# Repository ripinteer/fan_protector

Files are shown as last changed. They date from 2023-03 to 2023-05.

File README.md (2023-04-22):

# Fan Protector
Simple polulu-compatible protection board for Xiaomi/Roborock radial fans

### A word about all that hustle
>Remote cooling systems are becoming a trend in the field of high-end 3D printers. You install a big and powerful turbine somewhere on the printer and connect it to the tool head using a lightweight and flexible hose that you can purchase as a spare part for CPAP medical devices.
>
>Some DIY projects utilize big 7040 blowers for that purpose. 7040 is a BLDC fan with an external control board which is sold as a kit. Has pretty much power and costs about 50$ (which is quite steep for this kind of product imho)
>
>Turns out there are compact fans for robot vacuum cleaners, widely available on Aliexpress and other places as a spare parts. Provided in the refurbished condition they are five times cheaper than 7040, and still have comparable potential.

So if you want to adapt cheap (10$) and powerful vacuum cleaner turbines to your CPAP cooling system you can just connect PWM and DC to it... ~~Most likely it will burn your electronics and finally set you free from 3D printing addiciton~~ <br> **However, this type of connnection is strongly prohibited**, as it may (**will**) **fry** your **equipment** due to lack of certian passive components which is expected to be at the motherboard side.

For more details about XiaoFans aka Roborockers, please refer to <a href="https://github.com/condottab/Roborock-CPAP" target="_blank">this repo from a friend of mine</a>

My take on that situation
---
So, to make use of XiaoFan, good folks designed a simple schematic that adds missed protection features and stabilizes control voltage. To simplify the installation process and eliminate wiring "fun" I designed this simple polulu-compatible protection board, based on the original schematic.

<figure>
    <p align="center">
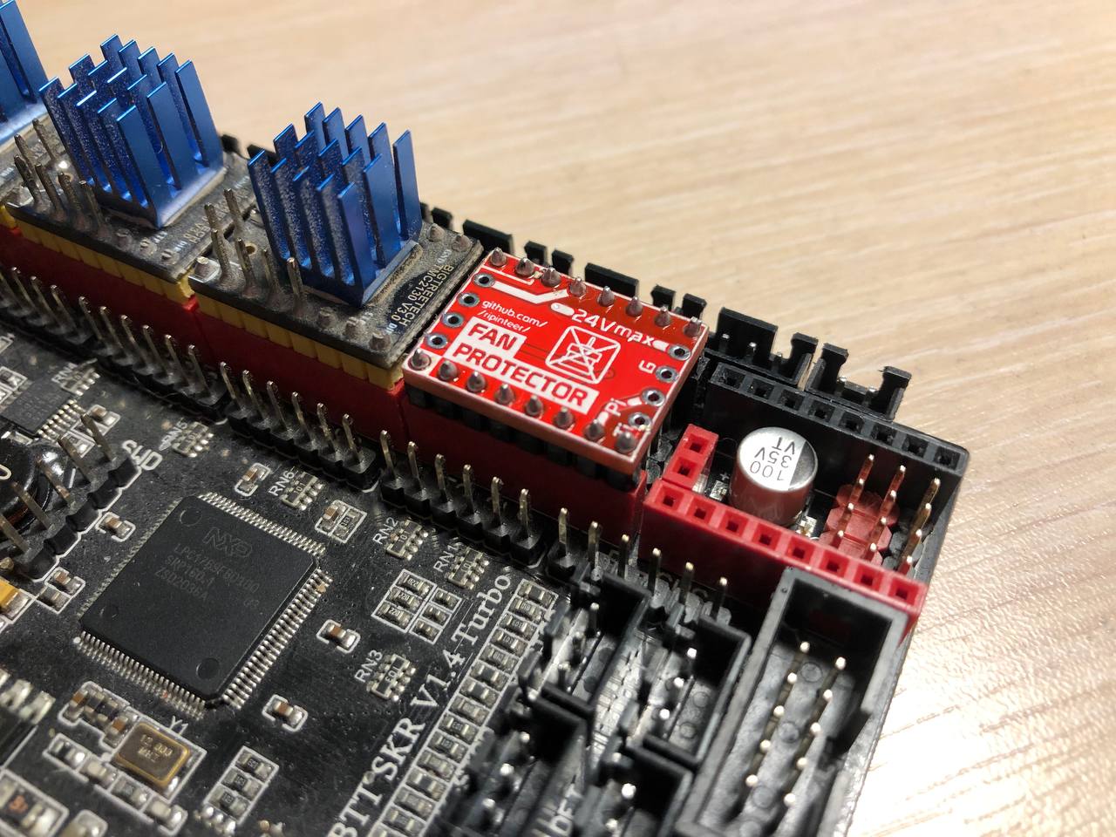
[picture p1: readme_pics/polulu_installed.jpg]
protector installed in polulu socket
        
    </p>
    <figcaption> <p align="center">As description suggests, protector can be installed right in the driver socket of the motherboard</p></figcaption>
</figure>

Once the board is installed, the corresponding 4pin XH2.54 motor connector becomes the protected fan connector. **It will use the same power source your steppers powered from, so keep that in mind.** The XiaoFan is rated 15V max, but it can be overvolted to 24V and tuned down to ~60% using PWM to continious run. 

> :pushpin: **Note:** This fan is a beast, so 60% of it will be already overkill for some cases

However, if you are reading this, you probably want to squeeze all from the XiaoFan setup, and this won't be a problem. Just to be safe you can provide some sort of cooling to the cooling fan (haha). The 40mm fan can be a way to go (refer to the link in the beginning).

### Connecting to Klipper
Nothing too complicated, just add another fan section. You can find examples for Qinatsu and Nidec (indicated at blower PCB) fans by using link above. 

* #### For polulu connection
you will need to know STEP and DIR pin addresses for the driver slot, where Fan Protector is installed. STEP pin serves as PWM and DIR serves as FG pin (tachometer, probably useless, and will be moved to another pin in Fan Protector v2.0 for Nidec workaround)

* #### For inline/"classic" connection
you will need to connect three (four with FG) pins: GND, VDD (aka VDD aka "plus"), and PWM. The XiaoFans is pretty powerhungry (~2.5A at 24V 100%) so you should power it from the main DC supply (PSU). PWM pin should be connected to any unoccupied PWM-controllable output on the motherboard. Ideally, this pin should support hardware PWM, so you can go for higher frequencies to eliminate "whistle" caused by low-freq PWM. Klipper should warn you if the chosen pin is unsupported by hardware PWM. <br> *Also this type of connection is already described in the repo by the link above which should be considered prior*

<figure>
    <p align="center">
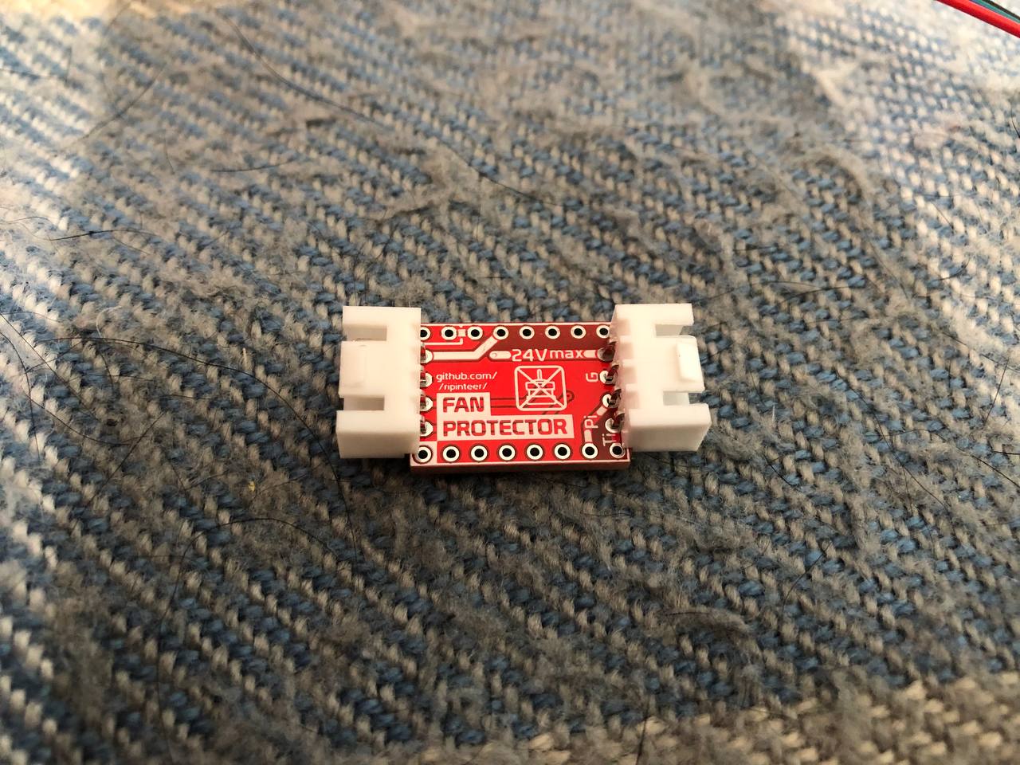
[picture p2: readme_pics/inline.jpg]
protector board with XH2.54 connectors installed
        
    </p>
    <figcaption><p align="center">Protector board with soldered XH2.54 connectors</p></figcaption>
</figure>

### Connecting to Marlin

Not yet tested/proved, but should be done with pin remapping according to scheme. TODO

---

### The Nidec case
As you can see, making use of this kind of tech comes with certain bumps. This time, it's Nidec fan tricky startup sequence. For some reason, they require a PWM signal to be present when powering it up. In other words, the PWM signal and DC power should be supplied together at the same moment. If not, Nidec won't start. Thankfully, Klipper comes with `enable_pin:` functionality, therefore we can just put a MOSFET in the DC circuit and tell Klipper about it.<br>
The only problem is my design doesn't have this MOSFET. "Why?" you ask. :eye:4:goat: <br>... Well, I guess that's what ver2.0 is for <br>
However! This only means that Nidec XiaoFans aren't supported by polulu configuration, but classic connection scheme is still viable. <br> No, lol. <br> **Nidec fans aren't supported at all (at least now)**, I need to finish *fan_protector v2.0* based on my custom scheme ASAP. <br> ~~For now you can power the fan through the one of exsiting heater MOSFETs on the motherboard, like additional heater port, which should be capable of driving 2.5+ Amps continuously. Set it's pin as `enable_pin:` in Klipper, connect the PWM and you should be good to go~~
> :pushpin: **Note:** As you can probably notice, this design supports both polulu and standart connection. Let's consider standart connection a default variant by now. 

<figure>
    <p align="center">
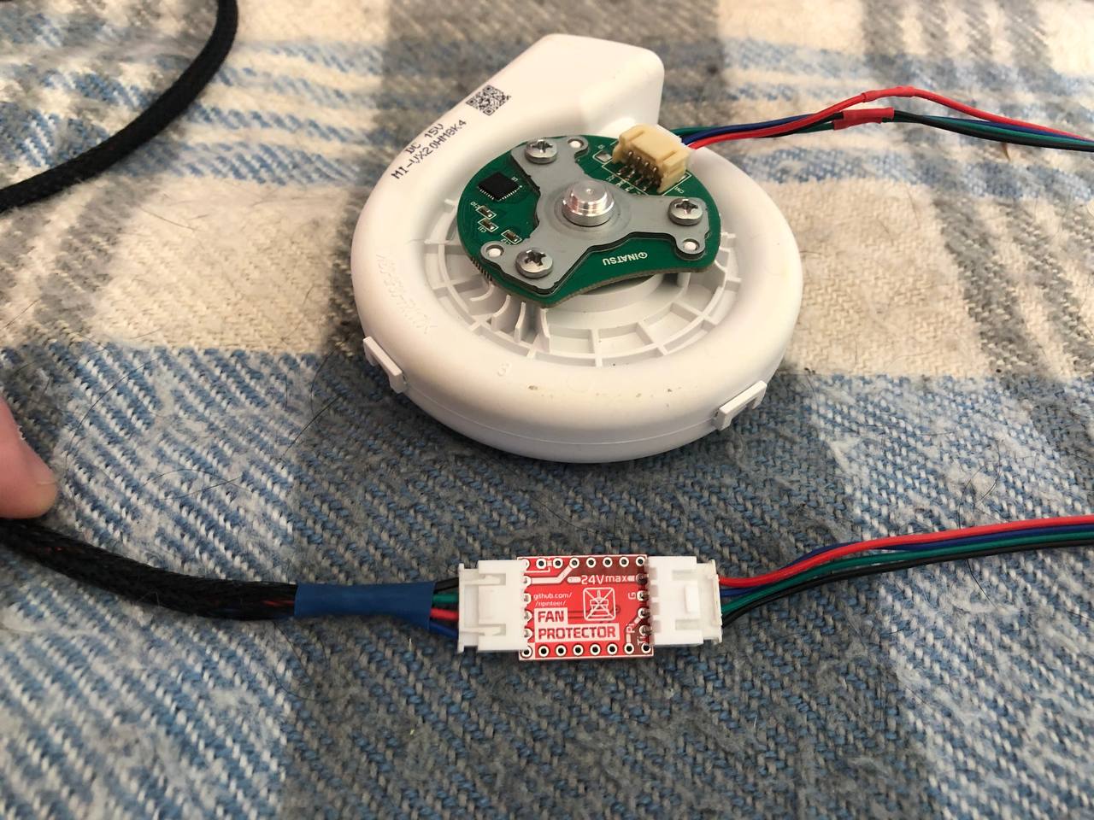
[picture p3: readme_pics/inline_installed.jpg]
Protector installed inline
        
    </p>
    <figcaption><p align="center">Inline connection example</p></figcaption>
</figure>

Any use of the provided files is at your own risk!

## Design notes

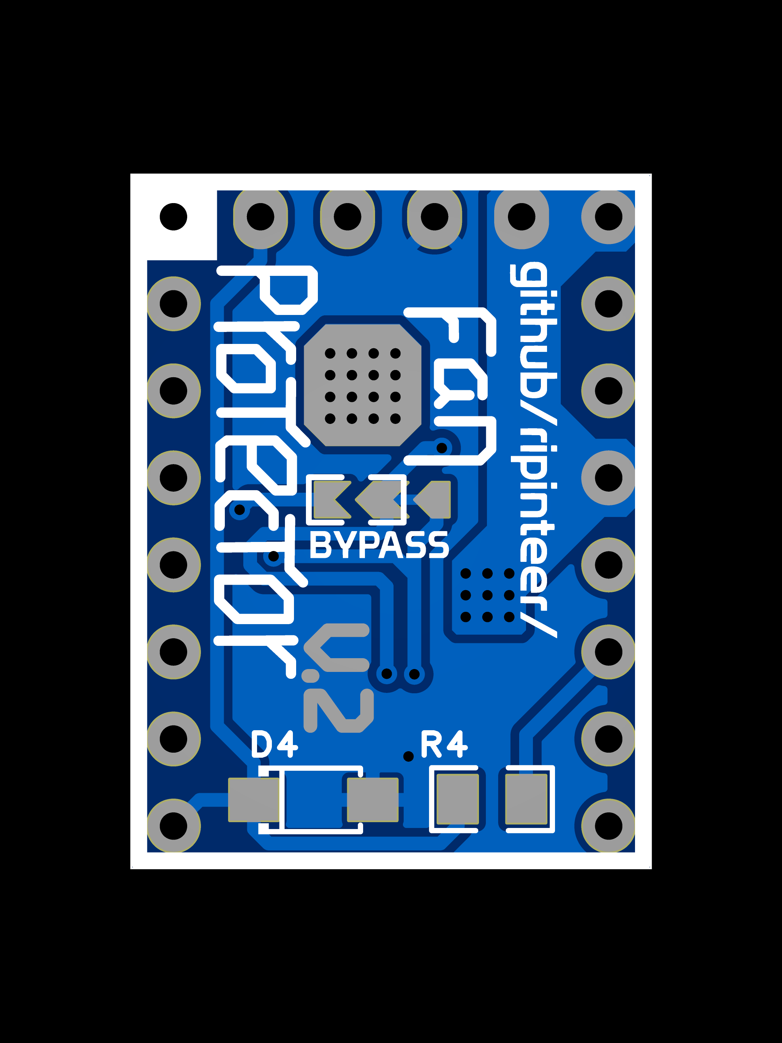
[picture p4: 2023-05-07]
readme_pics/top.png

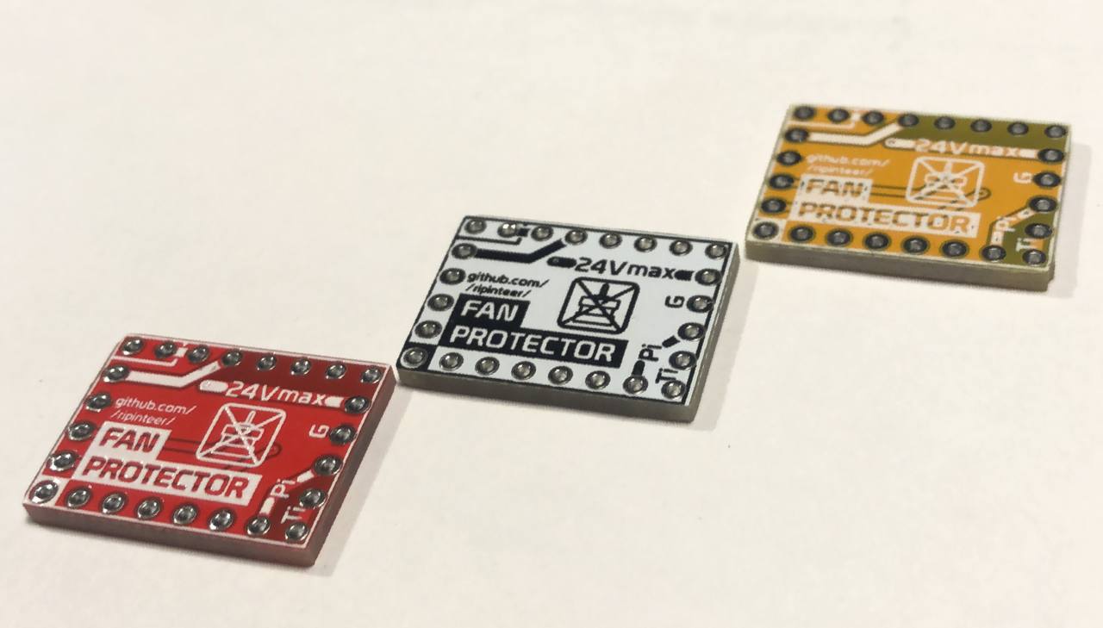
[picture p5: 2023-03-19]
readme_pics/board_colors.jpg

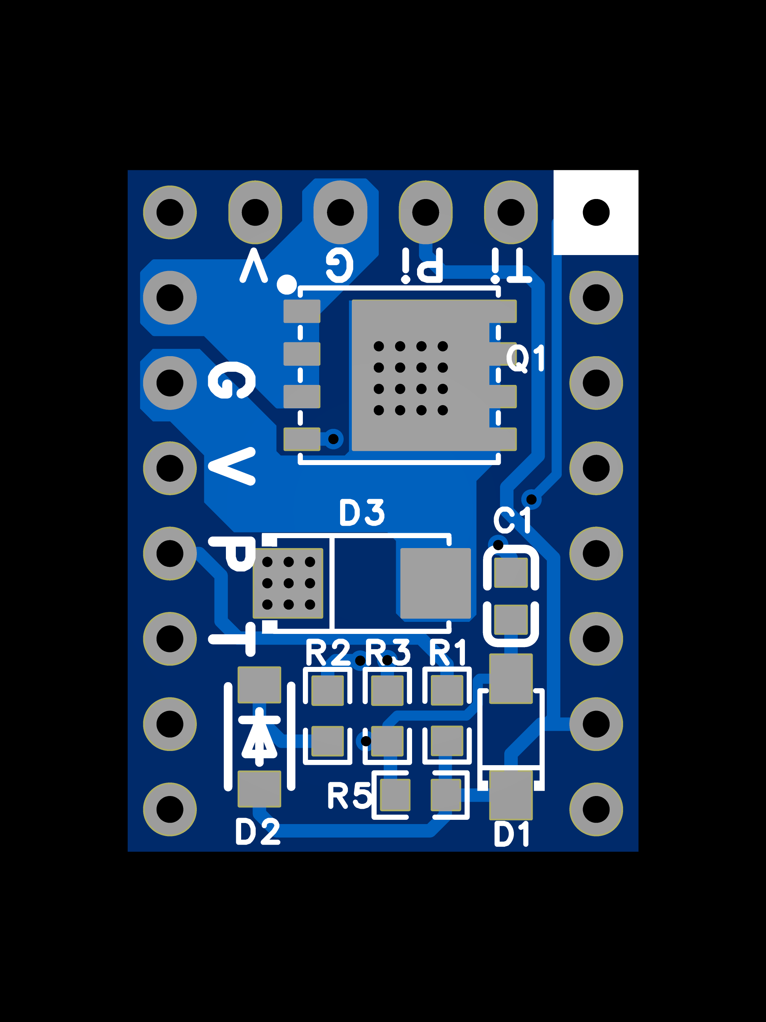
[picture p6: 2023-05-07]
readme_pics/bottom.png

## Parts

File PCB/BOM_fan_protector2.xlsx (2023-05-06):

No. | Quantity | Comment | Designator | Footprint | Value | Manufacturer Part | Manufacturer | Supplier Part | Supplier | Name | LCSC Stock | JLCPCB Stock
1 | 1 | 100nF | C1 | C0603 | 100nF |  |  |  |  | 100nF
2 | 2 | SMF5.0A | D1,D4 | SOD-123FL_L2.7-W1.8-LS3.8-RD |  | SMF5.0A | FUXINSEMI(富芯森美) | C908213 | LCSC | SMF5.0A | 79580 | 1586
3 | 1 | 1N5819W | D2 | SOD-123F_L2.8-W1.8-LS3.7-RD |  | 1N5819W | 晶导微电子 | C169540 | LCSC | 1N5819W | 65300 | 53973
4 | 1 | DO-214AC | D3 | SMA_L4.3-W2.6-LS5.2-RD |  | DO-214AC |  | C9900026895 | LCSC | DO-214AC |  | 0
5 | 1 | HY1904C2 | Q1 | DFN-8_L5.9-W5.2-P1.27-LS6.2-BL |  | HY1904C2 | HUAYI(华羿微) | C358116 | LCSC | HY1904C2 | 250 | 271
6 | 2 | 1K | R1,R2 | R0603 | 1K |  |  |  |  | 1K
7 | 1 | 1M | R3 | R0603 | 1M |  |  |  |  | 1M
8 | 1 | 1K | R4 | R0805 | 1K |  |  |  |  | 1K
9 | 1 | 10K | R5 | R0603 | 10K |  |  |  |  | 10K

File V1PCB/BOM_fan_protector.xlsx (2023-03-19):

No. | Quantity | Comment | Designator | Footprint | Value | Manufacturer Part | Manufacturer | Supplier Part | Supplier | Name
1 | 1 | 1N5819WS | D1 | SOD-323_L1.6-W1.3-LS2.7-RD |  | 1N5819WS | TWGMC(台湾迪嘉) | C727116 | LCSC | 1N5819WS
2 | 3 | BZT52C10S | D2,D3,D4 | SOD-323_L1.6-W1.3-LS2.7-RD |  | BZT52C10S | 晶导微电子 | C353563 | LCSC | BZT52C10S
3 | 1 | DO-214AC | D5 | SMA_L4.3-W2.6-LS5.2-RD |  | DO-214AC |  | C9900026895 | LCSC | DO-214AC
4 | 2 | 1K | R1,R3 | R0805 | 1K |  |  |  |  | 1K
5 | 1 | 10K | R2 | R0805 | 10K |  |  |  |  | 10K

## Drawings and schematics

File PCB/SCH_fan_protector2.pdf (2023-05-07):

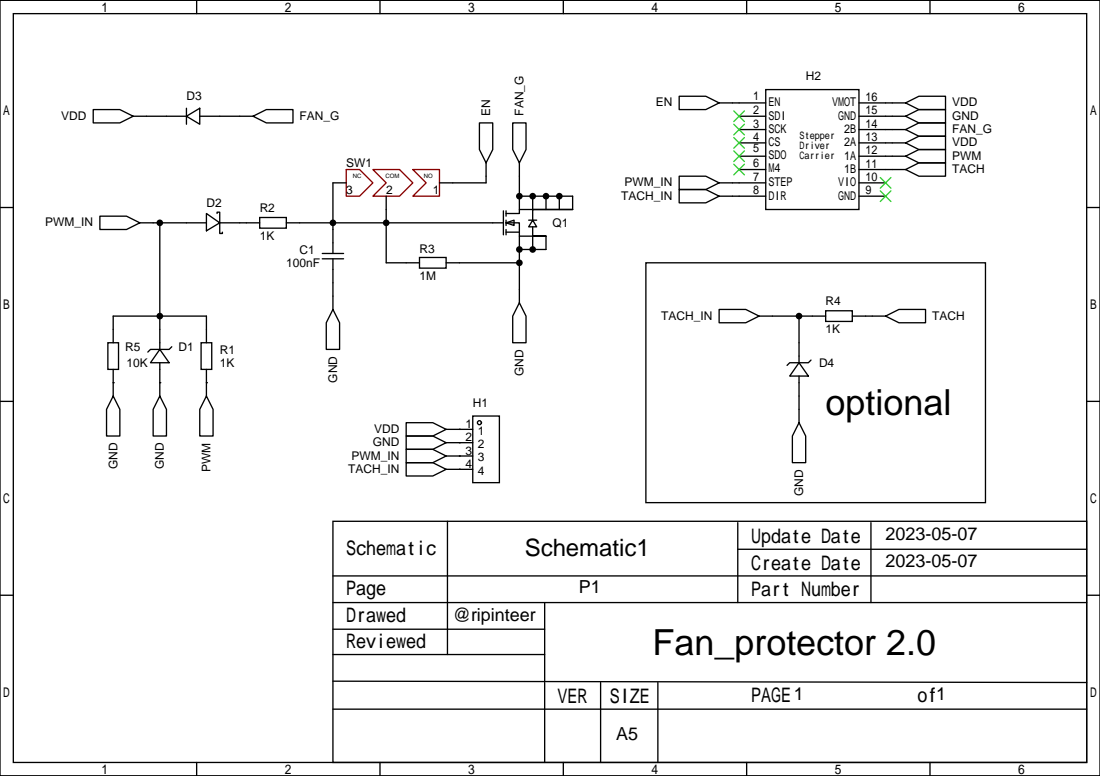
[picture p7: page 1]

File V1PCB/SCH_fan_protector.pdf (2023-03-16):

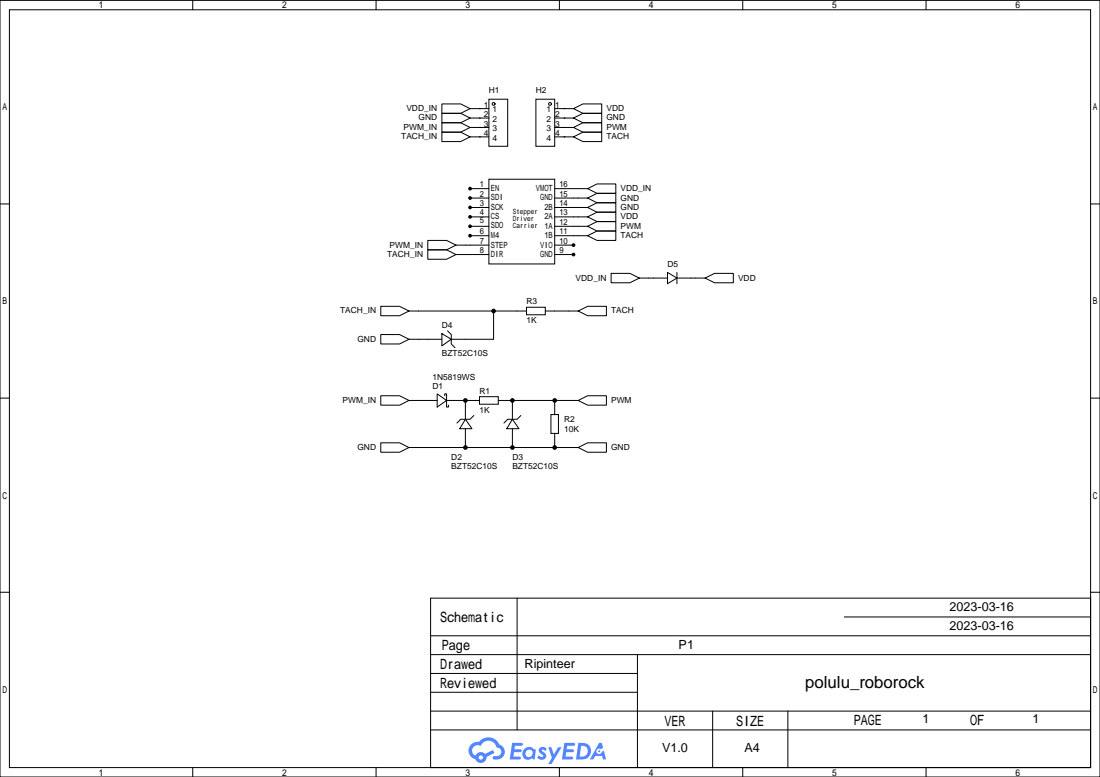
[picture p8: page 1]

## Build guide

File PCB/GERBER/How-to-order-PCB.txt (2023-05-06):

How to Order PCB

Please refer to:
https://docs.easyeda.com/en/PCB/Order-PCB

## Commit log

2023-03-16 Add fabraction data
    SHC, Gerber, BOM
    [BOM_fan_protector.xlsx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]
2023-03-19 Add photos, PNP (CPL) files and pics
    [BOM_fan_protector.xlsx, PickAndPlace_fan_protector.csv]
2023-05-06 v2 files added
    [BOM_fan_protector.xlsx, BOM_fan_protector2.xlsx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]
2023-05-07 structure update
    [BOM_fan_protector.xlsx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]
